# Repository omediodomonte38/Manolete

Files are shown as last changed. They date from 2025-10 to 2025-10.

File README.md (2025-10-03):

# Manolete
Manolete: Combat robot created for the OSHWDEM 2025 Antweight 1lb combat competition.

Created by:

[PHOTO here]

## Introduction

The design of Manolete 2025 is an iteration of Manolete 2024. The robot is a vertical spinner with an beater bar type weapon. Due to the weight of the 2024 model, for 2025 we decided to start from scratch and, instead of relying on 3D printing, we decided to use CNC mill or manually cut parts out of the raw materials, in order to reduce weight and increase strength. The weapon has been changed from plastic to aluminum to increase its destructive capacity.

## Parts
- [Wheel Motors (400rpm)](https://a.aliexpress.com/_EvYxx0i)
- [Weapon Motor (1200KV)](https://a.aliexpress.com/_EvVvyQE)
- [Screws (m2 y m3)](https://a.aliexpress.com/_EGK4m7c)
- [Heat-Inserts](https://a.aliexpress.com/_EweGZSe)
- [Belt (s3m-165-55T)](https://a.aliexpress.com/_EwXwIhg)
- [Pulley (s3m-15T)](https://es.aliexpress.com/item/1005007624969629.html)
- [Carbon fibre (1.5mm) — 10x11cm sheets](https://a.aliexpress.com/_Ey8keHu)
- [7075 aluminium (3.7 x 8 x 1.5 cm hollow piece)](https://www.randrade.com/recortes/1454-chapa-aluminio-en-aw-7075-t6-de-espesor-recortes.html)
- [Polycarbonate 5mm](https://www.randrade.com/recortes/1817-chapa-policarbonato-incoloro-espesor-recortes.html)
- [Countersunk screws M4 of 1.5cm](https://rayteyper.es/)
- [Wheels (1/10 RC Car)](https://es.aliexpress.com/item/1005009454745832.html)
- O-rings, for shock absorption, graciously donated by Mateo's grandpa

## Manufacturing

### Sides a.k.a. "tenedores"/"forks"
Manolete's sides, colloquially known as the forks, are fundamental to the robot's strength. They are made from Lexan (polycarbonate), cut with the CNC milling machine [eshapeoko from bricolabs](https://www.bricolabs.cc/wiki/herramientas/eshapeoko). The STL can be found [here](3D/Side_Support_5mm.stl). The bottom part, much like the sides, is also made from polycarbonate

### Top and bottom plates
Manufactored from carbon fiber of 1.5mm of thickness, these plates confer the robot most of its rigidness. They have been manually measured and cut by us, using an axle grinder (Silicosis warning)

### Weapon
The weapon, the most relevant part of the robot, has been created from Aluminium 7075 for added hardness. From a solid block, we machined the shape using the [HBM BF 28 Profi Vario milling machine from bricolabs](https://www.bricolabs.cc/wiki/herramientas/fresadora_hbm_bf_28_profi_vario) in conjunction with a vertical drill, also from bricolabs. The weapon includes several screws to focus the hits and add reach to the weapon.

## Assembly

The sides and top plates are assembled using wood screws, threaded onto the polycabronate. For added shock absorption we added o-rings. The weapon motor is threaded, in the same way (wood screws) to an inner wall made of plycarbonate, placed in the middle of the robot chasis. The motor connects to the weapon using a s3m pulley with 3D printed gears, threaded onto the weapon. The weapon axle is a screw, fixed to the sides using nuts.

## Electronics

The robot is driven through a simple receiver with brushed motors (and corresponding esc) for both wheels, with simple tank-style driving, and a brushless motor for the weapon (also with corresponding esc).

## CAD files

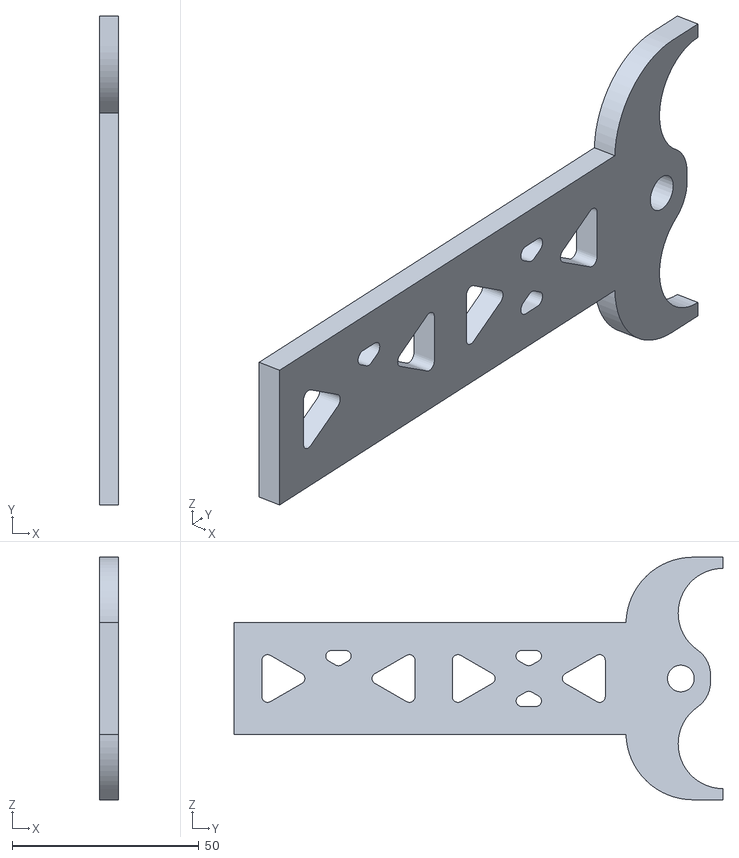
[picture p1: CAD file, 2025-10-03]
3D/Side_Support_5mm.stl
5.00 x 131.0 x 65.0

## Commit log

2025-10-03 Added stls
    [Side Support L 5mm reduced.stl]
2025-10-03 Refactored files
    [Side Support L 5mm reduced.stl, Side_Support_5mm.stl]
2025-10-03 Added stl in the readme
    Updated the README to correct section titles and links, and added a link to the STL file for the sides.
